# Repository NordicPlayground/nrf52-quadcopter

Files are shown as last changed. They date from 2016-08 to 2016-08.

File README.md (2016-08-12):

# nrf52-Quadcopter

This repository contains source files for the nRF52 Quadcopter, as described in [this blog post](https://devzone.nordicsemi.com/blogs/1005/nrf52-quadcopter/) on Nordic Semiconductor's [Developer Zone](https://devzone.nordicsemi.com).

To use the firmware, you need to put in the same folder as your copy of [SDK 11.0.0](https://developer.nordicsemi.com/nRF5_SDK/).

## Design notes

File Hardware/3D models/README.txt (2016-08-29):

Regarding 3D models for nRF Quadcopter

The ducts for the propellers are modeled to fit propellers of a particular diameter (the measurement eludes me at this time), 
and the clearance between the propeller and duct wall should be as small as possible

The ducts and motor holders are modeled to be printed on a machine with some inaccuarcies, 
so the planned friction fit might not be as tight when printed on another 3D printer.
This can be fixed by either changing the 3D files themselves or adding some electrical tape around the motors.

The battery holder is supposed to attach to the pin headers under the quadcopter,
holes in the "arms" of the holder need to be drilled. Preferrably as close to 0.7 mm as possible for a tight fit.

contact: martin.sivertsen@gmail.com

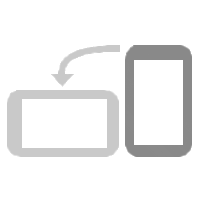
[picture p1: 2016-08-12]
Web/img/rotate.png

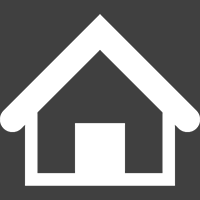
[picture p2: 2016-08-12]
Web/img/home.png

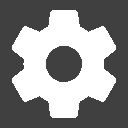
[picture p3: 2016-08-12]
Web/img/settings.png

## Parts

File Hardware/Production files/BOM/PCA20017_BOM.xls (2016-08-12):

Bill of material
PCB: | PCA20017
Version: | 1.0.0
Designator | Value | Description | Footprint Doc | Manufacturer | Manufacturer Part Number
A1 | 2450AT18B100 | 2.45 GHz chip antenna | 2450AT18B100 | Johanson Technology | 2450AT18B100
BAT | B2B-ZR | CONN JST 2POS 0.059" (1.50mm) | B2B-ZR | JST Sales America Inc | B2B-ZR(LF)(SN)
C1, C2, C11, C12 | 12pF | Capacitor, NP0, ±2% | 0402
C3 | 0.8pF | Capacitor, NP0, ±5% | 0402
C4, C5, C8, C15, C19, C21, C22, C23, C25, C26, C30, C32 | 100nF | Capacitor, X7R, ±10% | 0402
C6 | N.C. | Not mounted | 0402
C7 | 100pF | Capacitor, NP0, ±5% | 0402
C9, C31 | 4.7µF | Capacitor, X5R, ±10% | 0603
C10 | 1.0µF | Capacitor, X7R, ±10% | 0603
C13, C14, C18 | 1.0µF | Capacitor, X5R, ±5% | 0402
C16 | 4.7µF | Capacitor, X5R, ±20% | 0402
C17 | 22µF | Capacitor, X5R, ±10% | 0805
C20 | 10µF | Capacitor, X5R, ±20% | 0603
C24 | 10nF | Capacitor, X7R, ±10% | 0402
C27, C28 | 130pF | Chip Cap 0402 | 0402
C29 | 1.2pF | Capacitor, NP0, ±0.1pF | 0402
D1, D2, D3, D4 | BAT42W | Diode Schottky, Vr=30V, If=200mA, Vf=400mV, SOD-123 | SOD-123 | Multicomp | BAT42W
D5, D6 | ZLLS410TA | DIODE SCHOTTKY 10V 0.57A SOD323 | SOD-323 | Diodes Incorporated | ZLLS410TA
J1, J2, J3, J4 | Pin List 1x2 1.27mm | Pin List 1x2, 1.27mm (50mil), N.C. | LIST_1x2_TH_1.27mm_N.C.
J6 | MicroUSB-B | MicroUSB-B-SMT | USB-Micro-B-RA-SMD-PiP | Allen Creations Corp. | AJU55-BS2111-L
L1 | 3.9nH | Inductor, 170mA, ±0.1nH | 0402 | Murata | LQP15MN3N9B02D
L2 | 10µH | Inductor, 80mA, ±10% | 0603 | Taiyo Yuden | LBMF1608T100K
L3 | 15nH | Inductor, 320mA, ±5% | 0402 | Taiyo Yuden | HK100515NJ-T
L4 | 3.3nH | Inductor, 190mA, ±0.1nH | 0402 | Murata | LQP15MN3N3B02D
L5 | 2.7nH | Inductor, 220mA, ±0.1nH | 0402 | Murata | LQP15MN2N7B02D
LD1, LD1B, LD2, LD2B, LD3, LD3B, LD4, LD4B | LED RGB | RGB LED 1.00 mm x 1.00 mm SMD | SML-LX0404SIUPGUSB | Lumex | SML-LX0404SIUPGUSB
Q1, Q2, Q3, Q4 | PMV31XN | N-channel TrenchMOS FET | SOT23 | NXP | PMV31XN
R1, R20, R30 | 1k | Resistor, ±1%, 0.063W | 0402
R2, R3, R6, R7 | 100R | Resistor, ±1%, 0.063W | 0402
R4, R5, R8, R9, R12, R21, R23, R25, R36 | 10k | Resistor, ±1%, 0.063W | 0402
R10, R10B, R16, R16B, R28, R28B, R33, R33B | 2k2 | Resistor, ±1%, 0.063W | 0402
R11, R11B, R17, R17B, R31, R31B, R34, R34B | 680R | Resistor, ±1%, 0.063W | 0402
R13, R14, R29 | 4k7 | Resistor, ±1%, 0.063W | 0402
R15, R15B, R18, R18B, R32, R32B, R35, R35B | 820R | Resistor, ±1%, 0.063W | 0402
R19, R22 | 12k | Resistor, ±1%, 0.063W | 0402
R24 | 150R | Resistor, ±1%, 0.063W | 0402
R37, R39 | N.C. | Not mounted | 0402
R38, R40 | 0R | Resistor, ±5%, 0.063W | 0402
SW1 | PTS840 GK SMTR LFS | Microminiature SMT Switch, Side Actuated | PTS840 Gx | C & K | PTS840 GK SMTR LFS
U1 | nRF52832-QFAA | Multi-protocol Bluetooth Low Energy, ANT and 2.4GHz proprietary system-on-chip | QFN-48 | Nordic Semiconductor | nRF52832-QFAA
U2 | MPU-9250 | 9-axis MotionTracking™ Device | QFN-24 | InvenSense | MPU-9250
U3 | MS5611-01BA03 | Accurate Pressure/Altitude and Temperature sensor with I2C and SPI interface | QFN-8 | Measurement Specialties | MS561101BA03-50
U4 | BQ24075 | IC SINGLE CELL USB LI-ION CHARGER | S-PVQFN-N16 | Texas Instruments | BQ24075RGTT
U5 | MAX17043 | IC FUEL FUAGE LI-ION | TDFN-8L-2x3mm | Maxim | MAX17043G+U
U6 | PCAL6408A | 8-bit I2C-bus I/O expander with interrupt output | XQFN-16 | NXP Semiconductors | PCAL6408AHK
U7 | TLV70230DBVT | IC REG LDO 3V 300MA SOT23-5 | SOT-23-5 | Texas Instruments | TLV70230DBVT
U8 | 24AA64F | IC EEPROM 64K with I2C interface TDFN-8 | TDFN-8 | Microchip | 24AA64T-I/MNY
U9 | LPS25H | MEMS pressure sensor: 260-1260 hPa absolute digital output barometer | HCLGA-10L | STMicroelectronics | LPS25H
X1 | 32MHz | XTAL SMD 2016, 32MHz, Cl=8pF, Tot: ±40ppm | XTAL_2016 | Kyocera | CX2016DB32000D0WZRC1
X2 | 32.768kHz | XTAL SMD 2012, 32.768kHz, 9pF, ±20ppm | XTAL_3215 | Seiko | SC32S-9.0PF20PPM

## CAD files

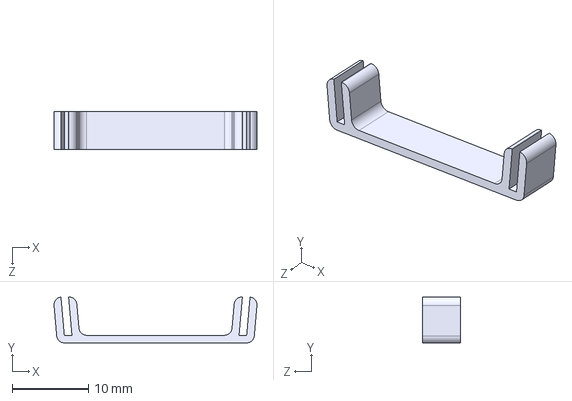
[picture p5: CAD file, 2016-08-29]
Hardware/3D models/Short duct stiffener.STEP
26.6 x 6.00 x 5.00 mm

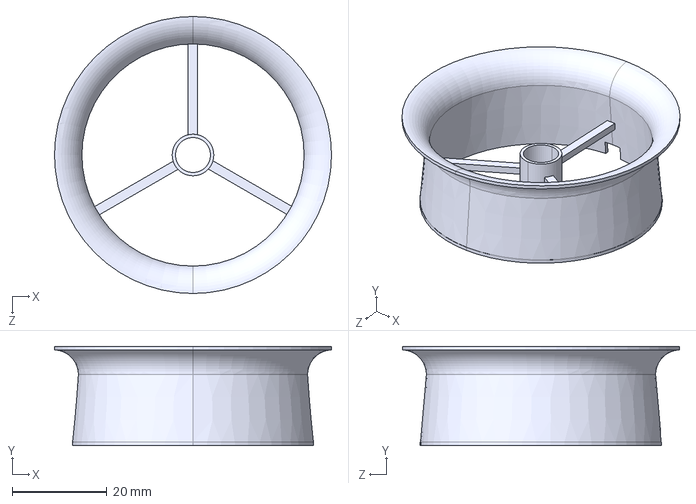
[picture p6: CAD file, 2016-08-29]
Hardware/3D models/3-blade prop and 7mm motor.STEP
58.6 x 21.0 x 58.6 mm

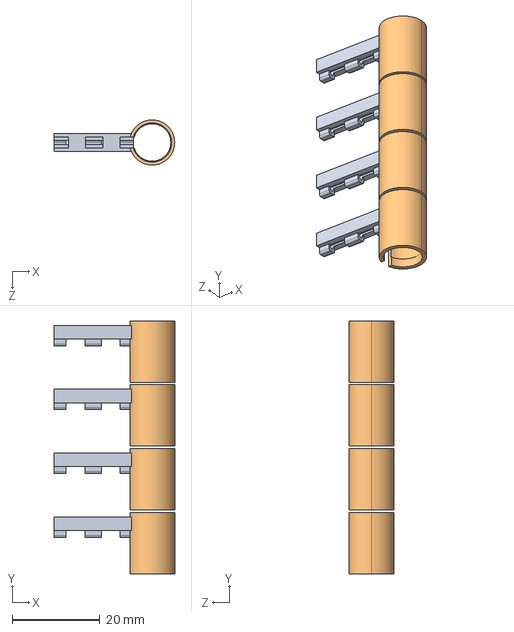
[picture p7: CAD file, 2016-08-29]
Hardware/3D models/8.5mm motorholders set of 4.STEP
27.4 x 57.5 x 10.3 mm
Arm without holder for motor x 4
Motor holder sylinder 8.45mm x 4

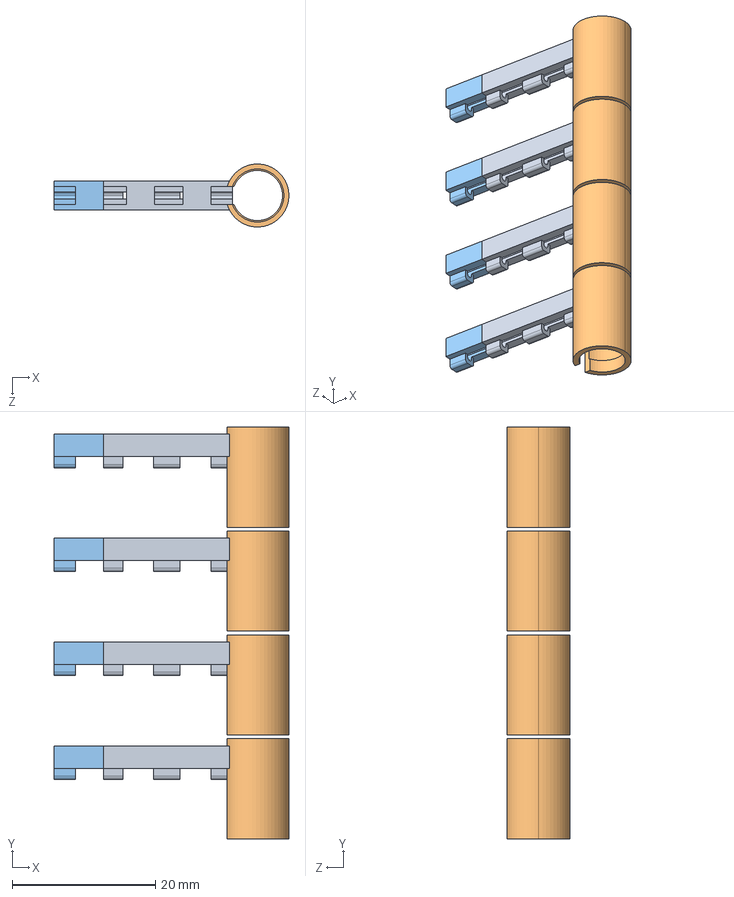
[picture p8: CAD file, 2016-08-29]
Hardware/3D models/7mm motorholders set of 4.STEP
32.8 x 57.5 x 8.79 mm
Arm without holder for motor x 4
Motor holder sylinder 7mm x 4
Arm without holder for motor extension x 4

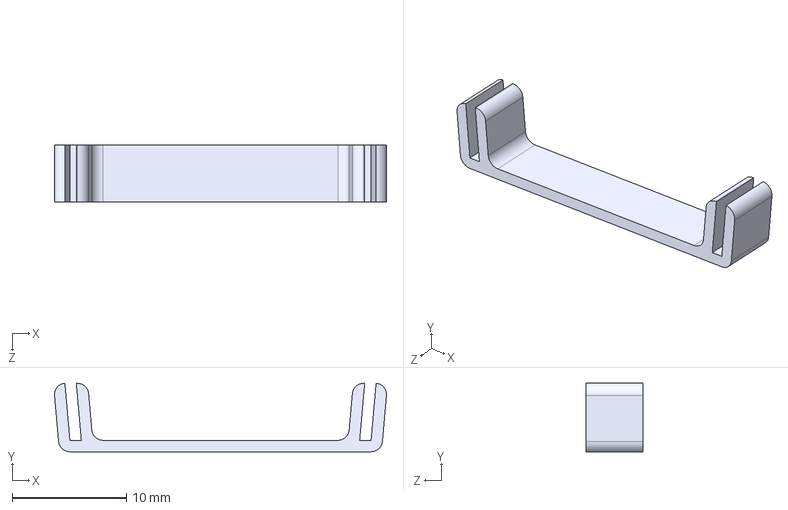
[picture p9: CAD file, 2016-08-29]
Hardware/3D models/Long duct stiffener.STEP
29.1 x 6.00 x 5.00 mm

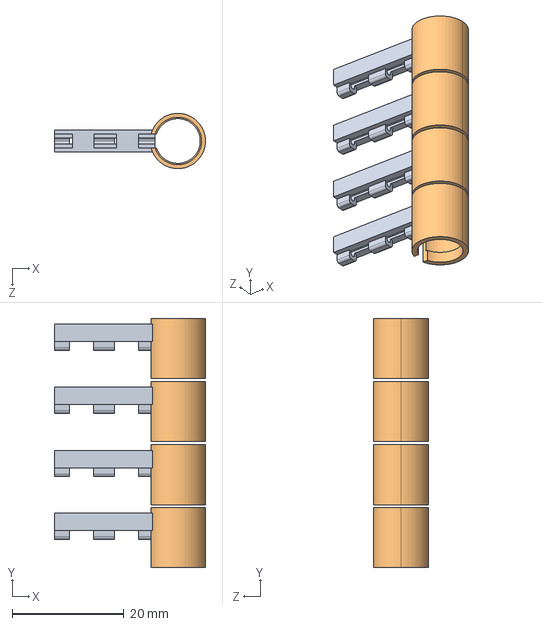
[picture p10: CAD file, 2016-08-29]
Hardware/3D models/8mm motorholders set of 4.STEP
27.0 x 44.5 x 9.90 mm
Arm without holder for motor x 4
Motor holder sylinder 8.1mm x 4

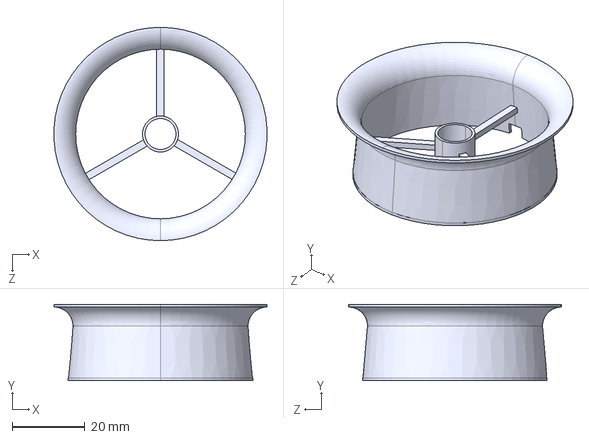
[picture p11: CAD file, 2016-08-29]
Hardware/3D models/3-blade prop and 8mm motor.STEP
58.5 x 21.0 x 58.6 mm

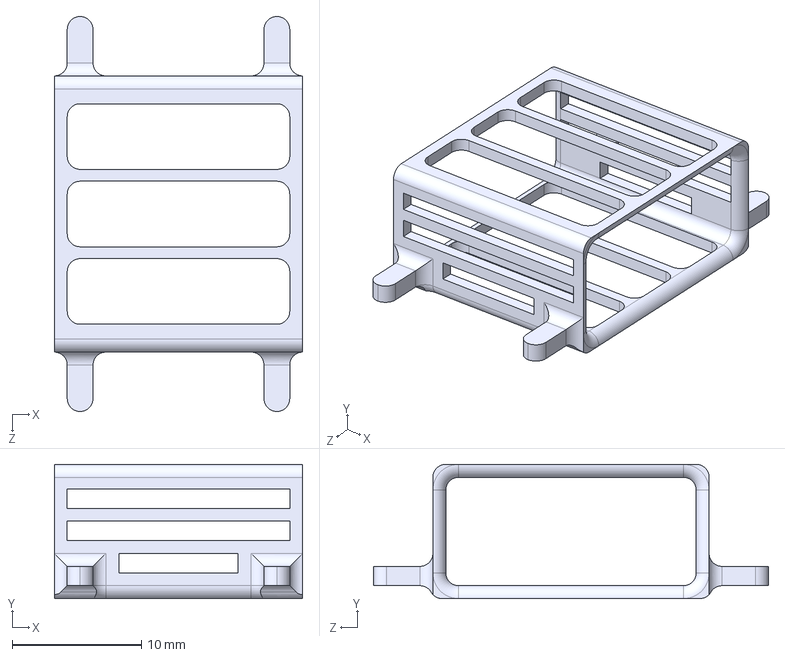
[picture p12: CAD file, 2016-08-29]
Hardware/3D models/Battery holder for 380mAh 25C.STEP
19.2 x 10.4 x 30.6 mm

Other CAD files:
Hardware/3D models/Long stiffener 7mm duct.STL
Hardware/3D models/3-blade prop and 8.5mm motor.STEP
Hardware/3D models/3-blade prop and 7mm motor.STL
Hardware/3D models/3-blade prop and 8.5mm motor.STL
Hardware/3D models/3-blade prop and 8mm motor.STL
Hardware/3D models/7mm motorholders set of 4.STL
Hardware/3D models/8.5 mm motorholders set of 4.STL
Hardware/3D models/8mm motorholders set of 4.STL
Hardware/3D models/Battery holder for 380mAh 25C.STL
Hardware/3D models/Short duct stiffener.STL

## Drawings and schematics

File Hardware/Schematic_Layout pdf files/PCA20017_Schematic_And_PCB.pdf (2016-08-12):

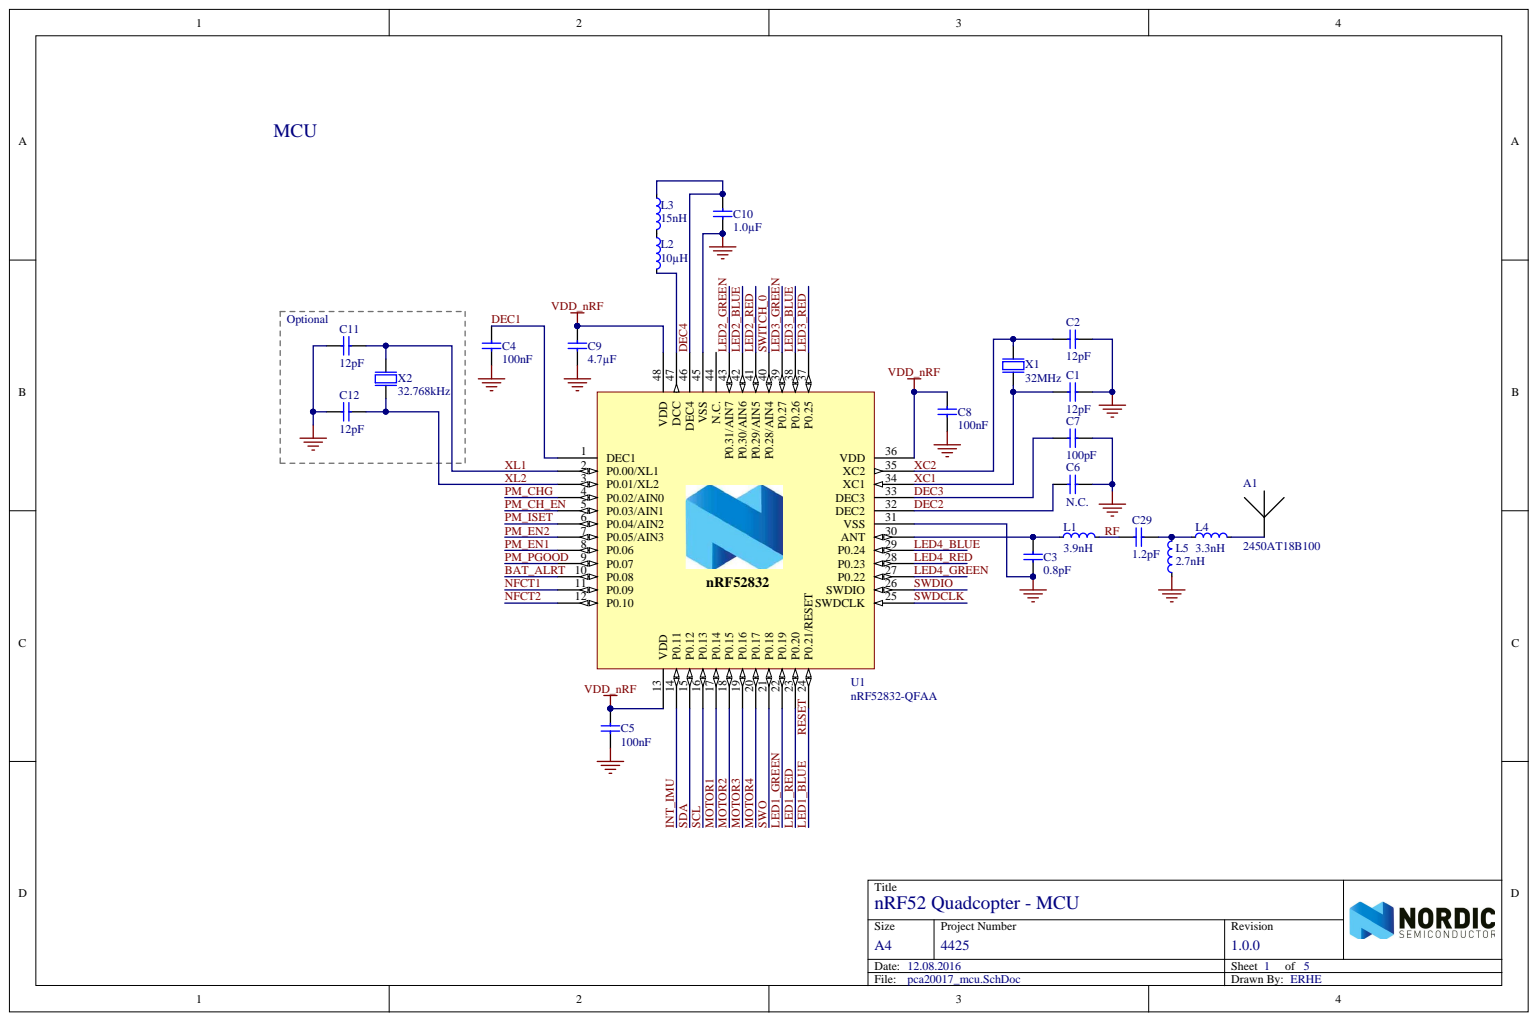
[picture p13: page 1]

P0.08 10 P0.09 11 P0.10 12 | | DEC3

DEC2

Title nRF52 Quadcopter - MCU

Size A4 | Project Number 4425 | Revision 1.0.0

Date: 12.08.2016 | Sheet of
File: pca20017_mcu.SchDoc | Drawn By: ERHE

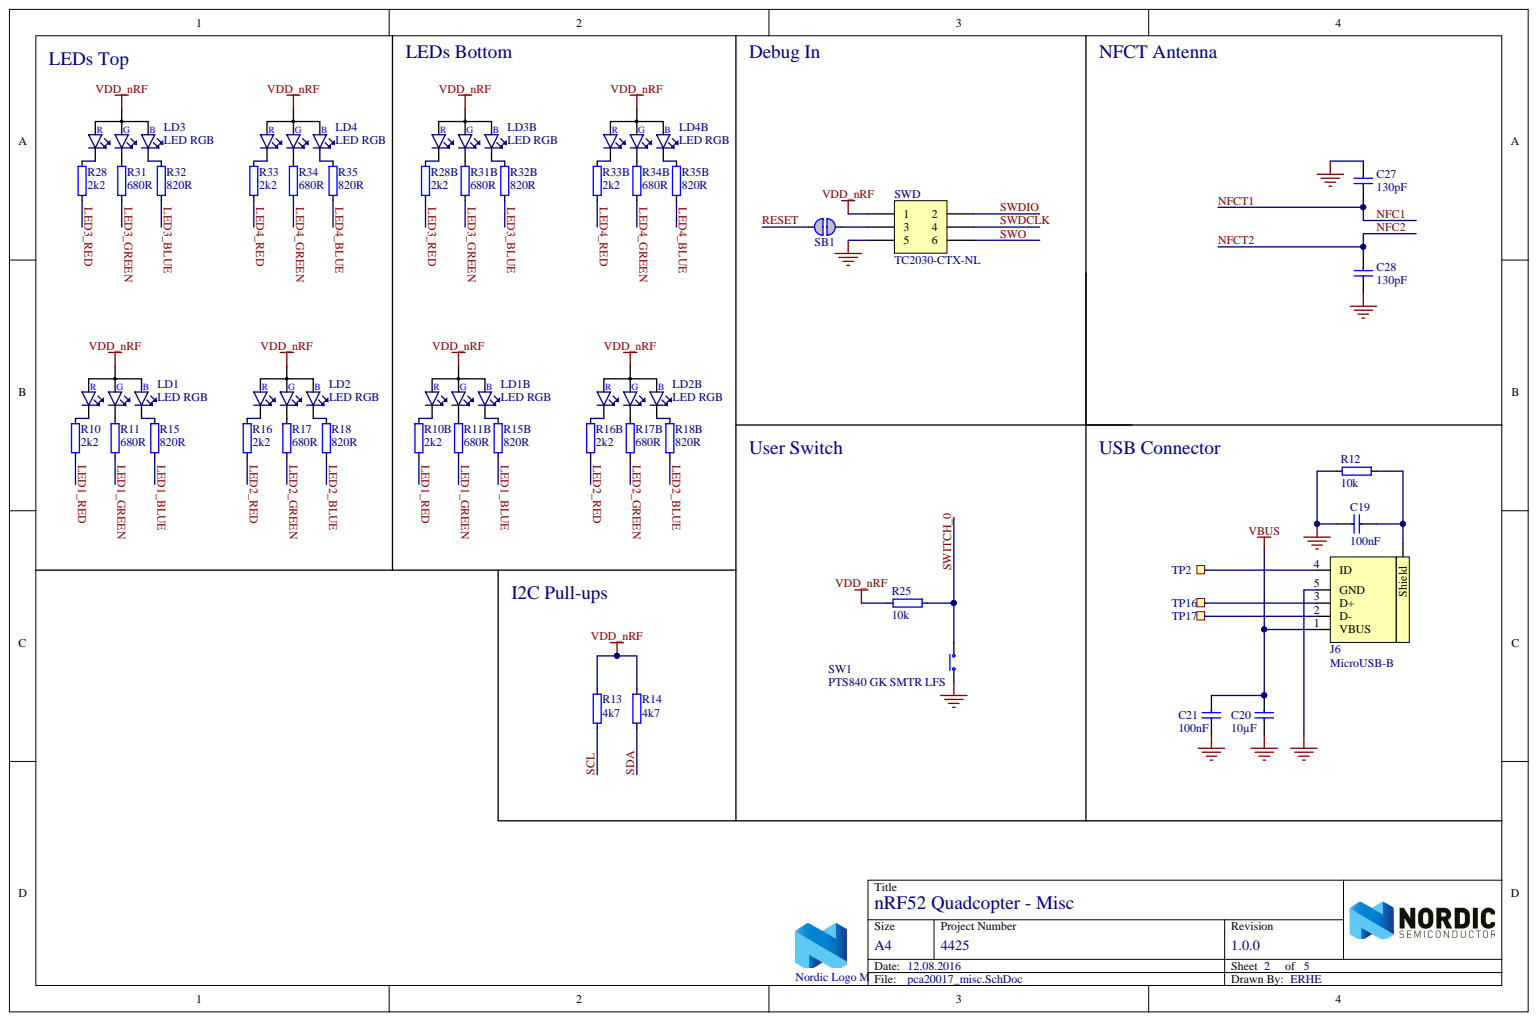
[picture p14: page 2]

ID 4
VBUS 1 D- 2 D+ 3 GND 5

Title nRF52 Quadcopter - Misc

Size A4 | Project Number 4425 | Revision 1.0.0

pca20017_misc.SchDoc

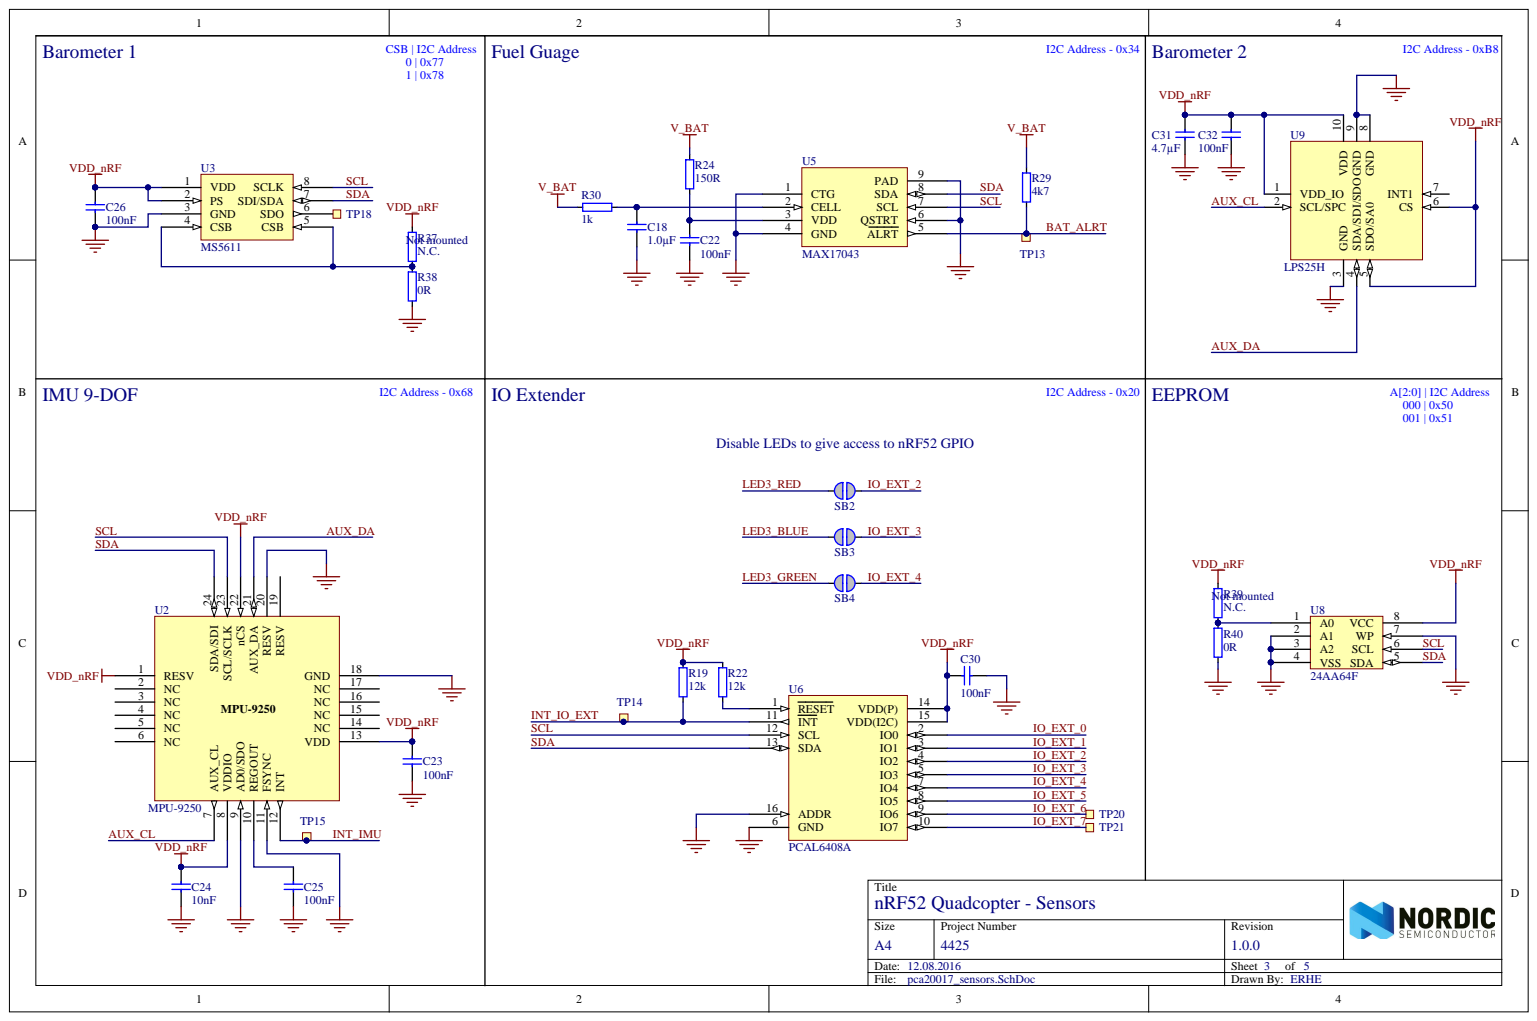
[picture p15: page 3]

SDO/SA0 5 SDA/SDI/SDO 4

VDD_IO 1

VDD 3

Disable LEDs to give access to nRF52 GPIO

Title nRF52 Quadcopter - Sensors

Size A4 | Project Number 4425 | Revision 1.0.0

pca20017_sensors.SchDoc

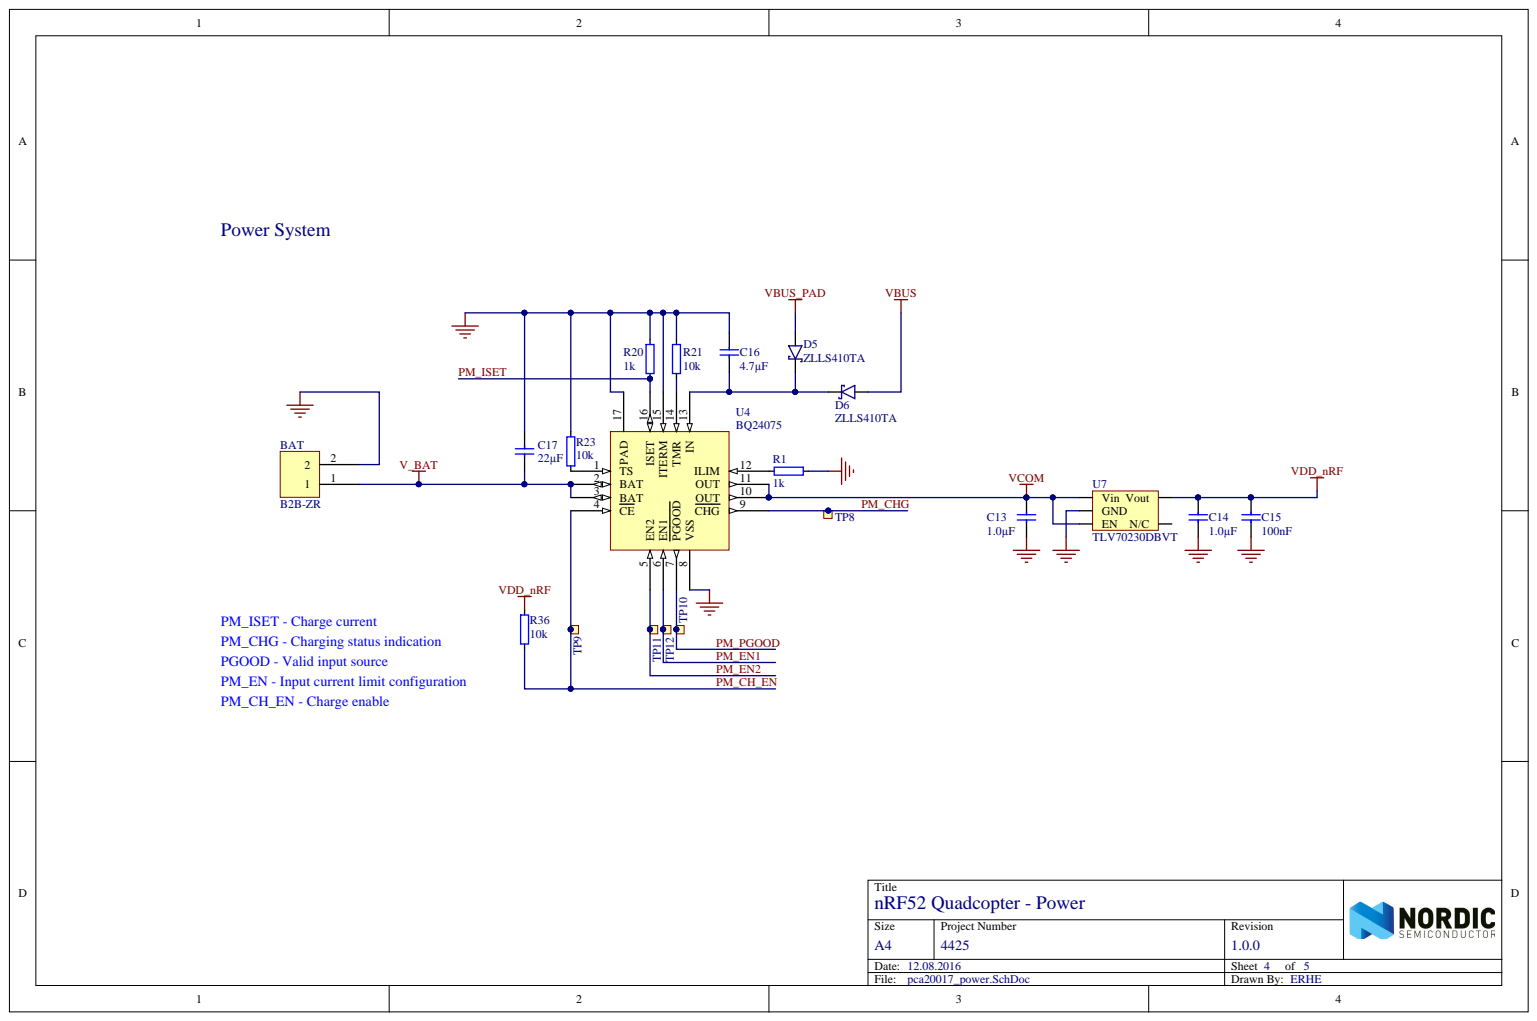
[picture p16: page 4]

IN 13 TMR 14 ITERM 15 ISET 16

PM_ISET - Charge current
PM_CHG - Charging status indication
PGOOD - Valid input source
PM_EN - Input current limit configuration
PM_CH_EN - Charge enable

Title nRF52 Quadcopter - Power

Size A4 | Project Number 4425 | Revision 1.0.0

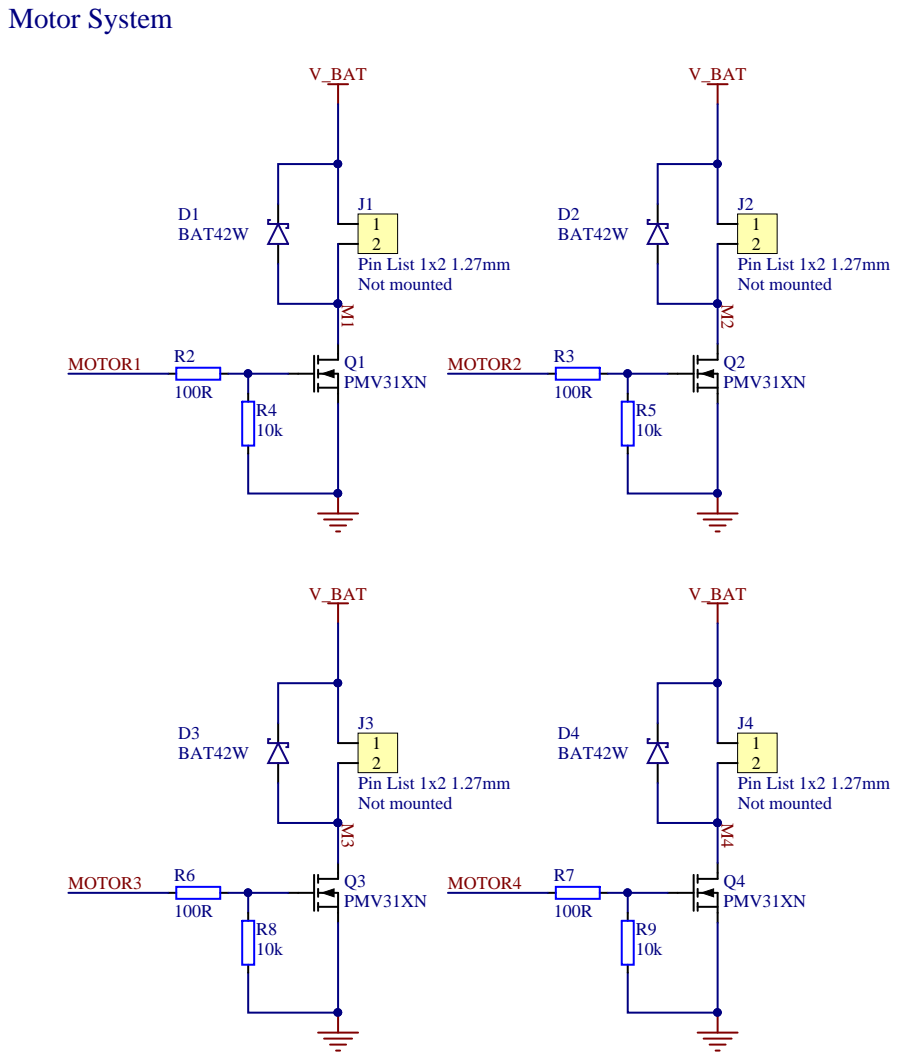
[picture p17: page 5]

Title nRF52 Quadcopter - Motors

Size A4 | Project Number 4425 | Revision 1.0.0

pca20017_motors.SchDoc

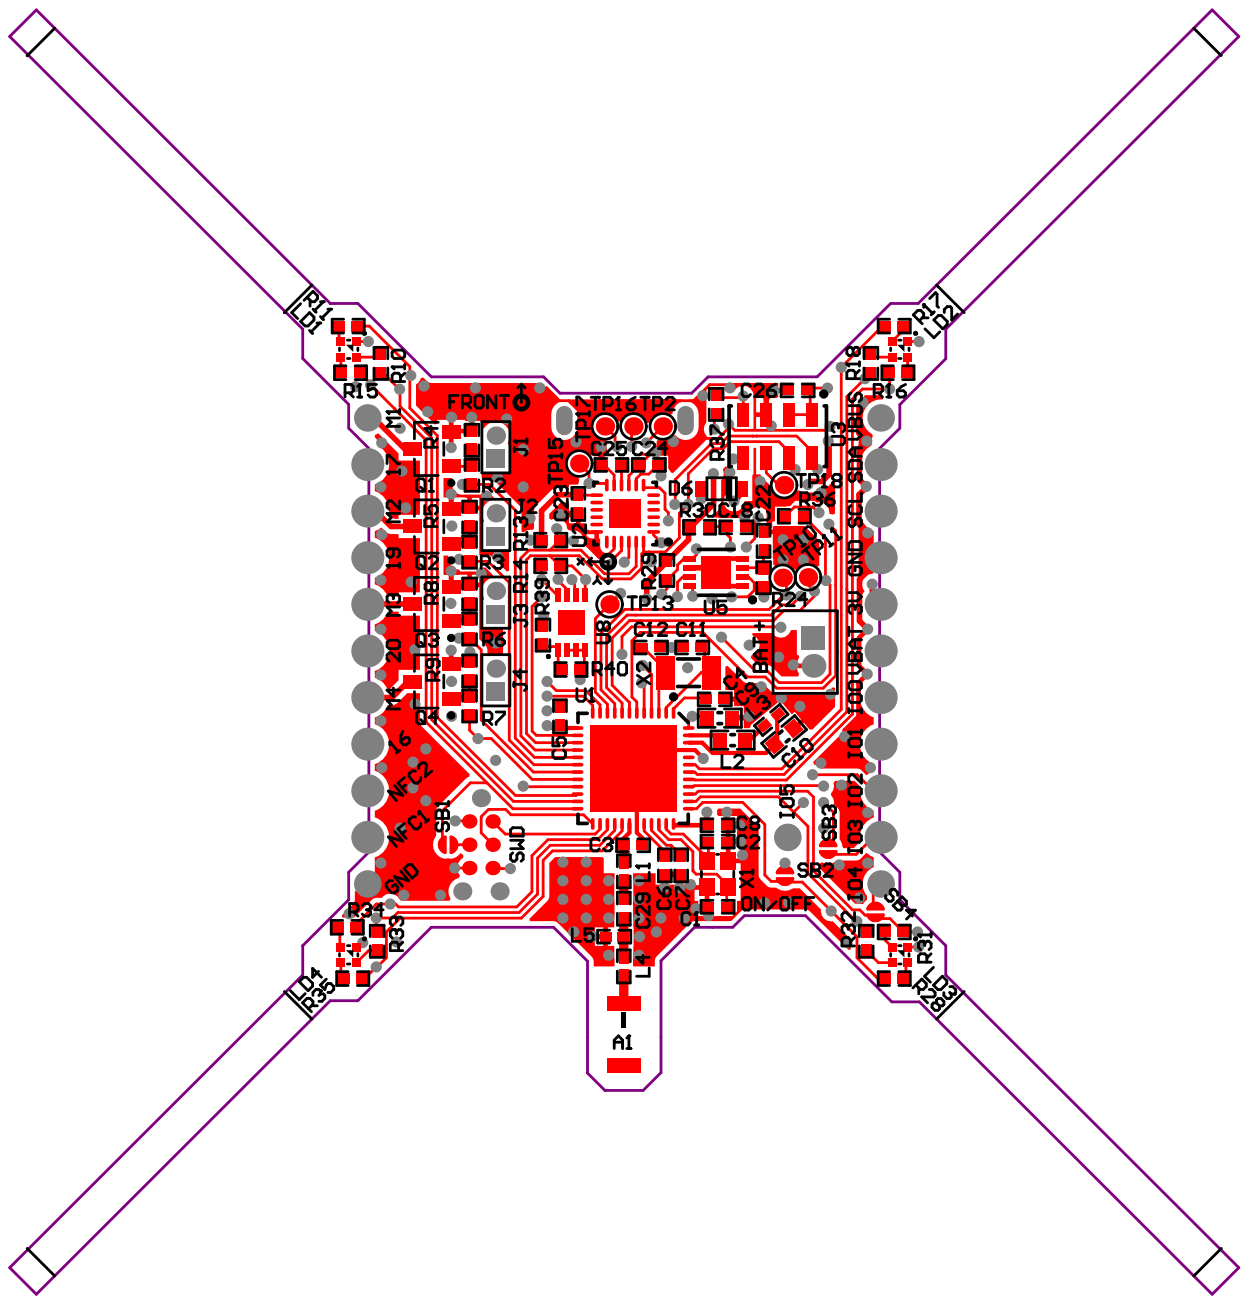
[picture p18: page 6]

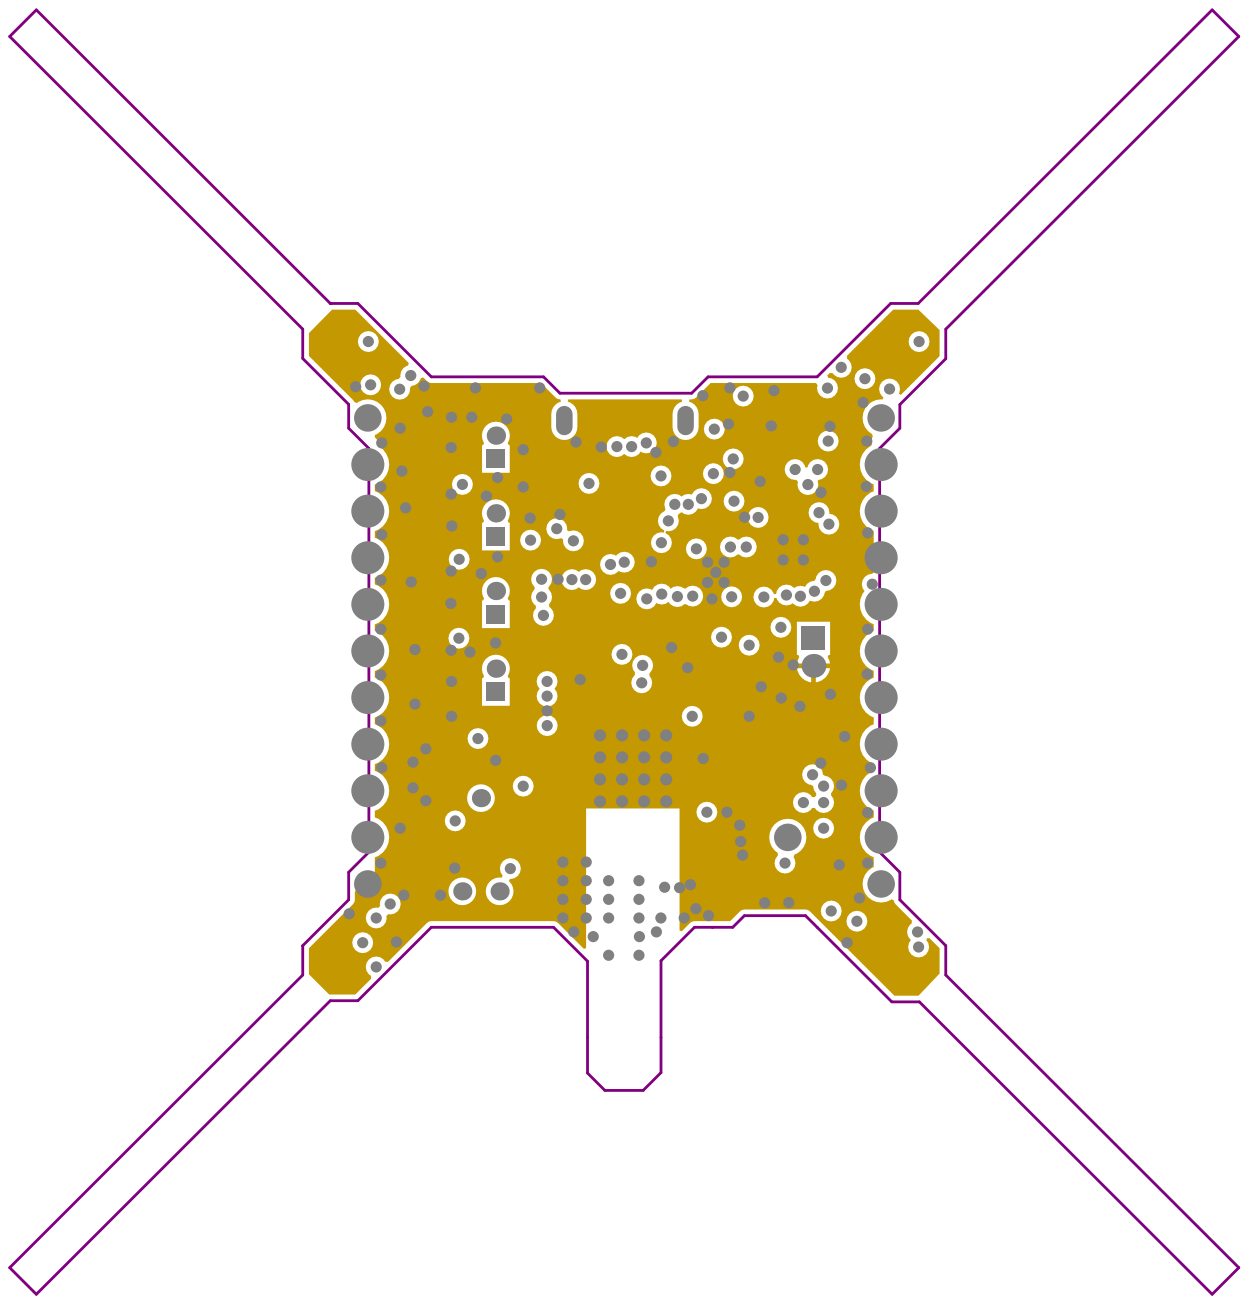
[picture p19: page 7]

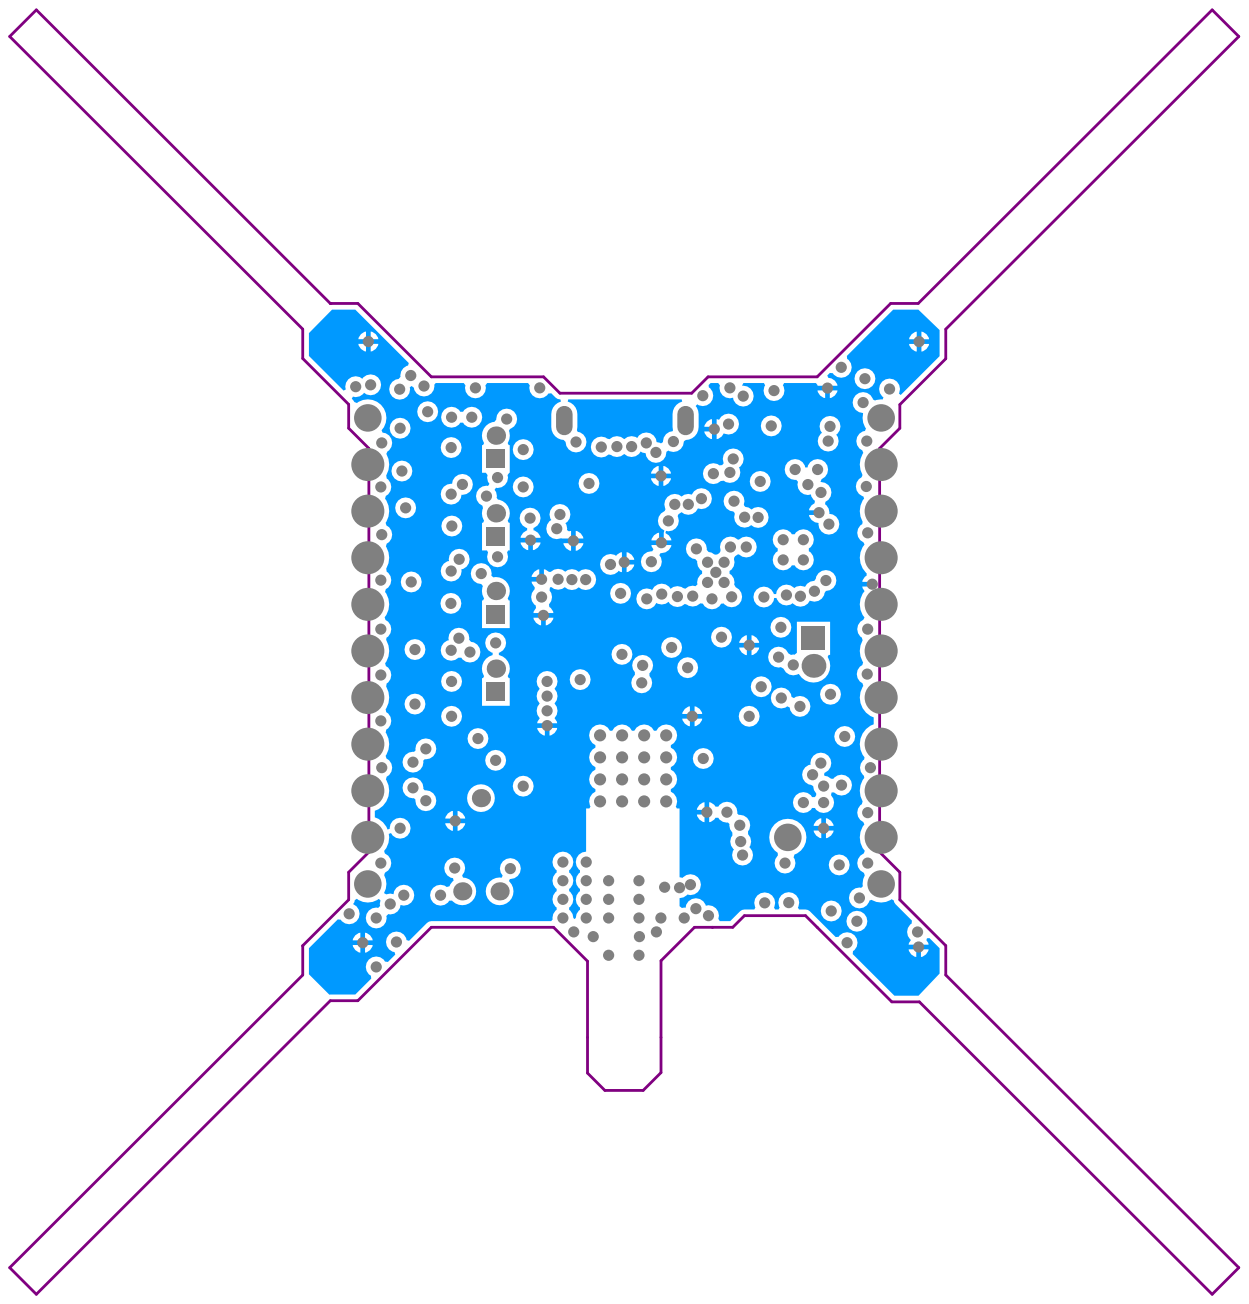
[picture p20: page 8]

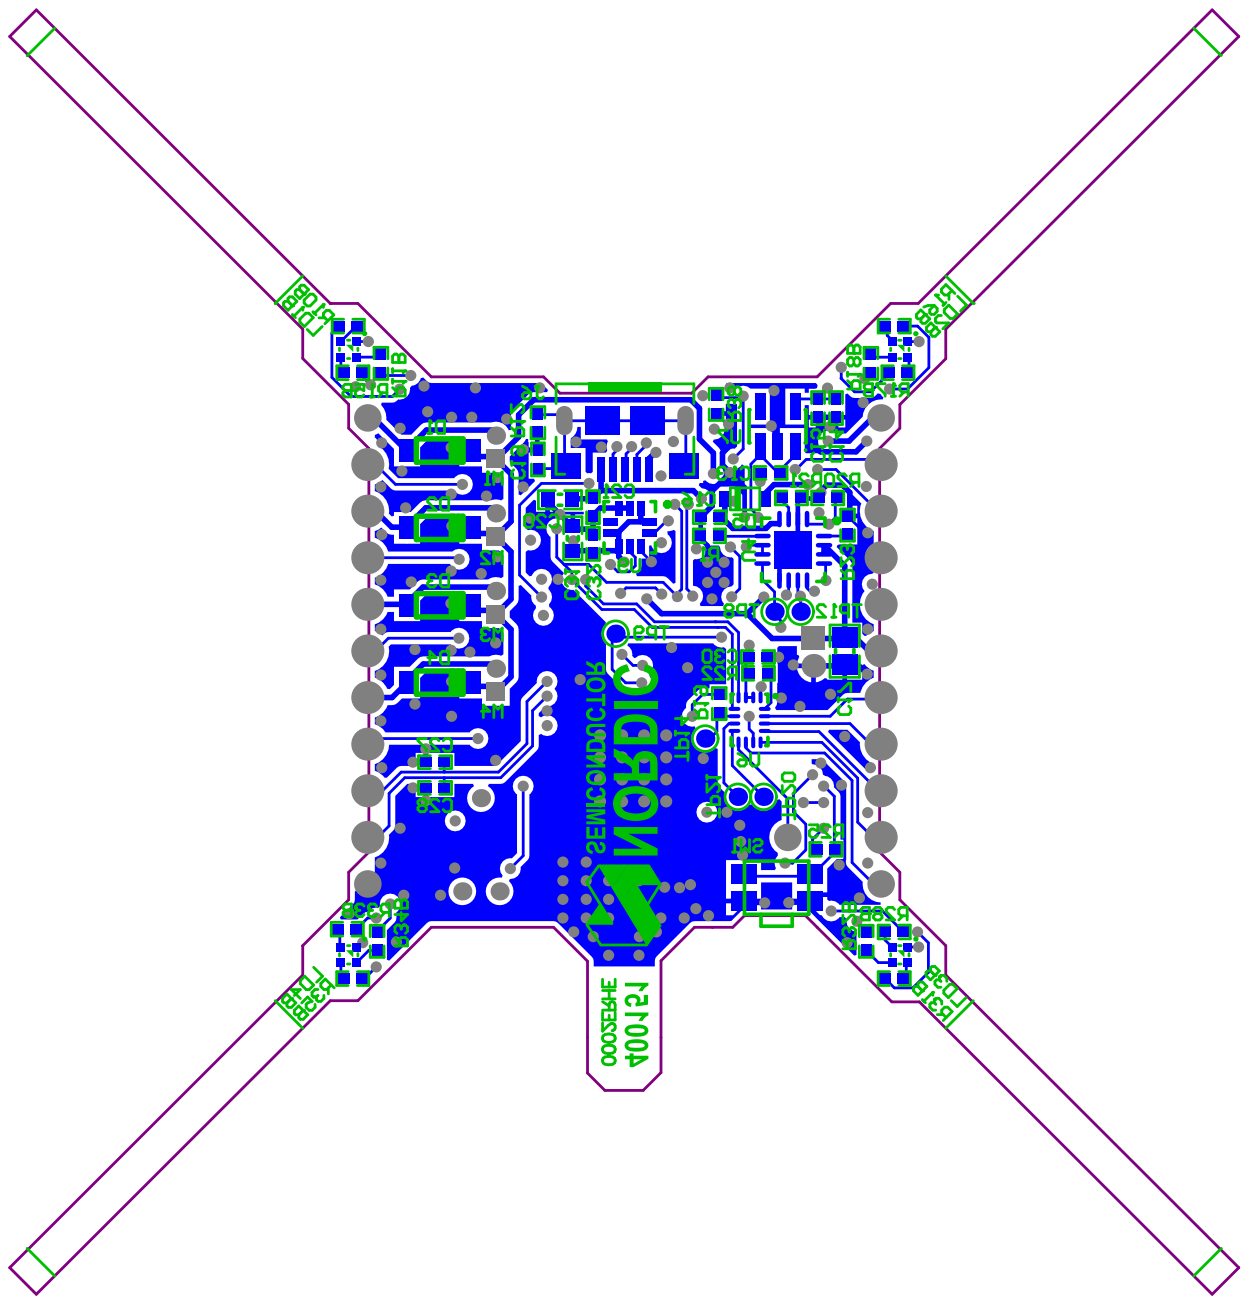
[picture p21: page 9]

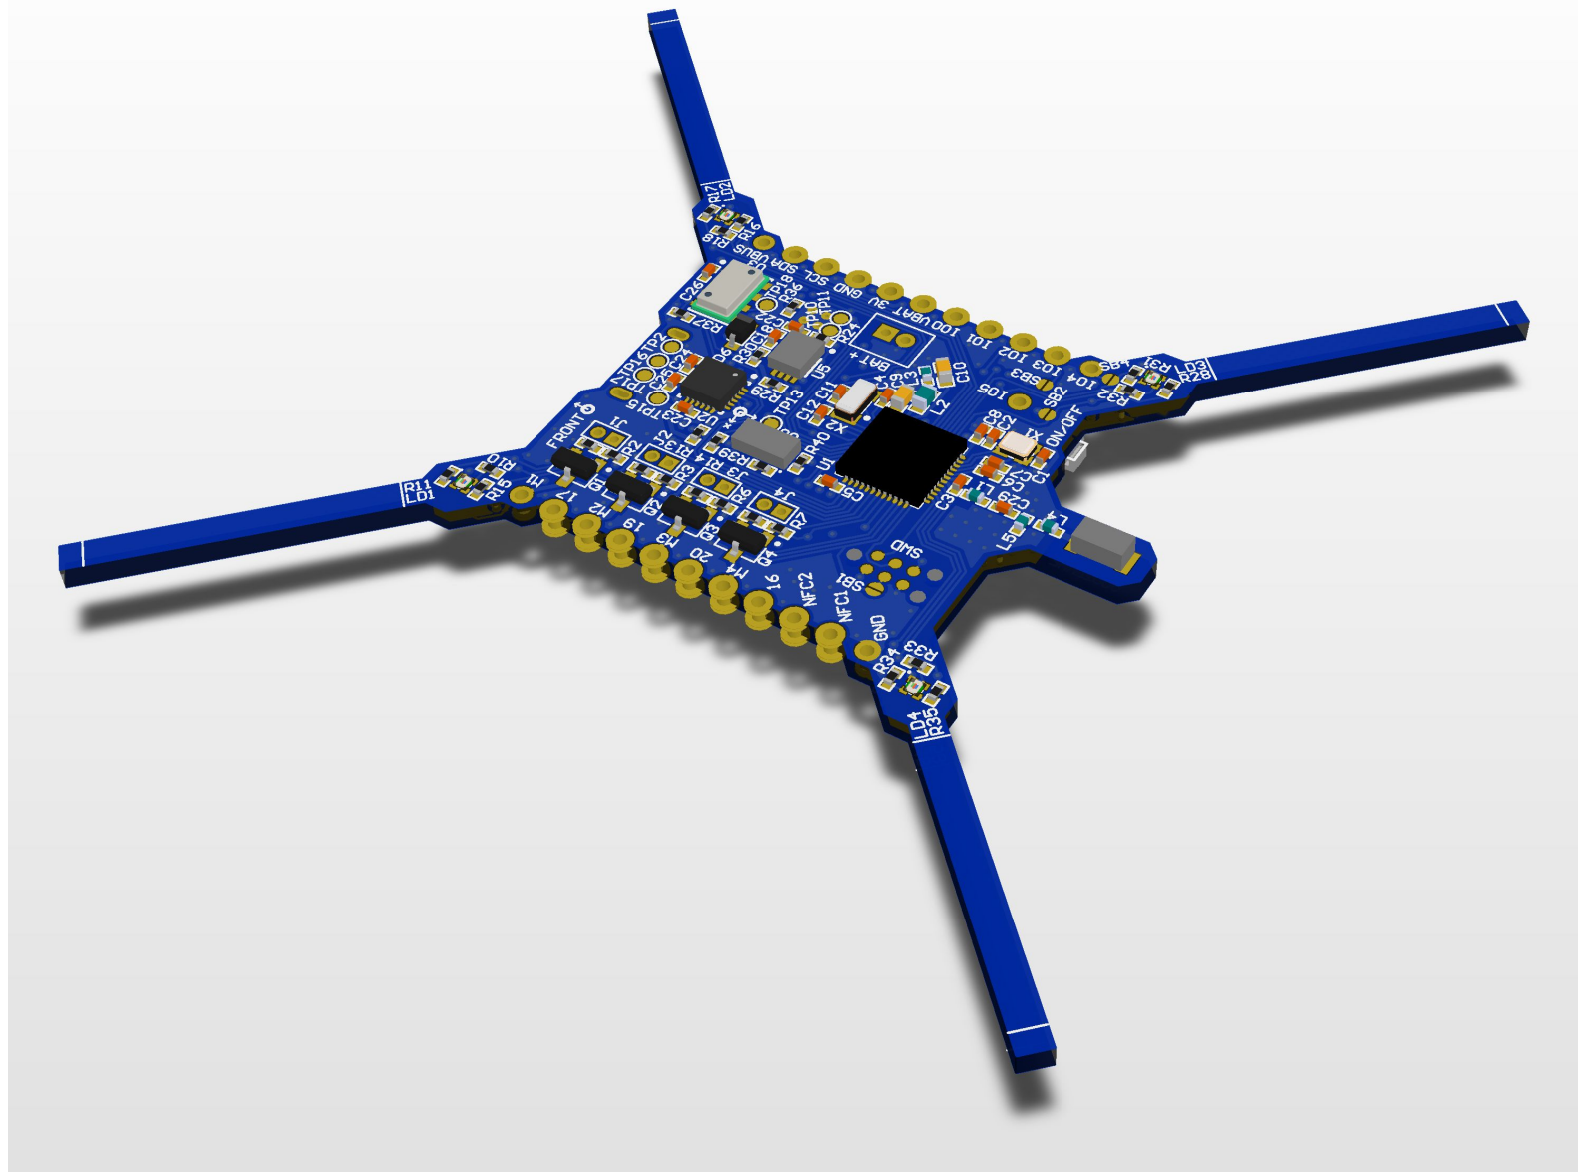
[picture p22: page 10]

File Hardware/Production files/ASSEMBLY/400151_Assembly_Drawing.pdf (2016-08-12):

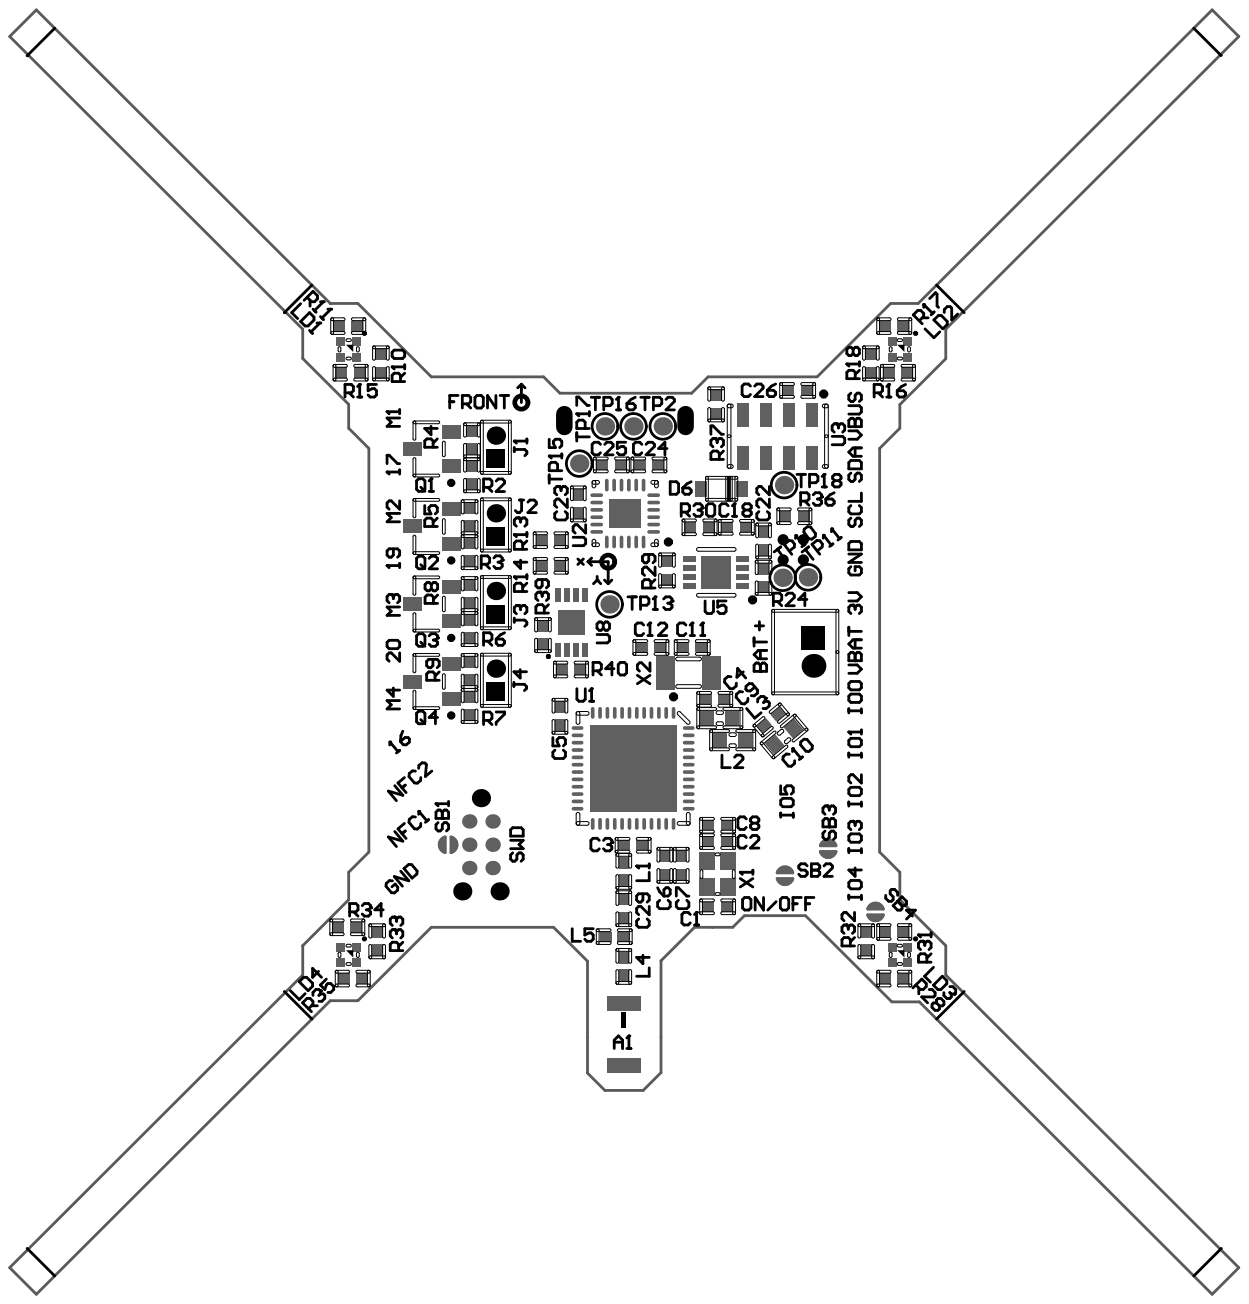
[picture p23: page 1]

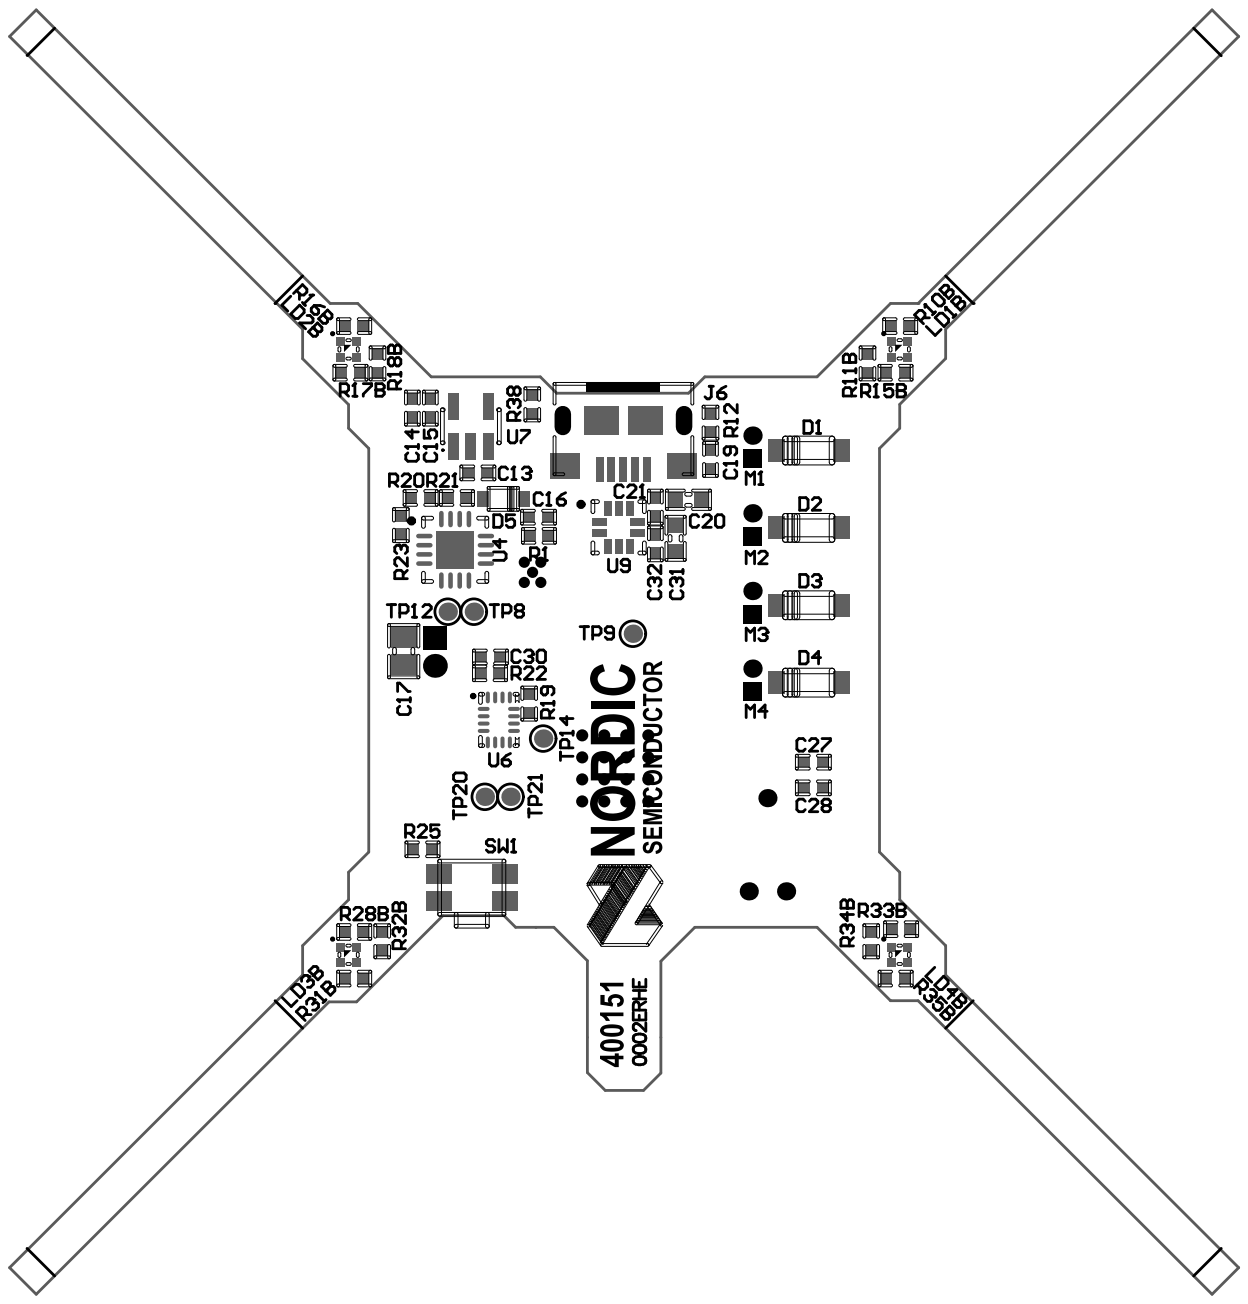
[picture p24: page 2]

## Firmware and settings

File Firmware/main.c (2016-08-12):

/* Copyright (c) 2014 Nordic Semiconductor. All Rights Reserved.
 *
 * The information contained herein is property of Nordic Semiconductor ASA.
 * Terms and conditions of usage are described in detail in NORDIC
 * SEMICONDUCTOR STANDARD SOFTWARE LICENSE AGREEMENT.
 *
 * Licensees are granted free, non-transferable use of the information. NO
 * WARRANTY of ANY KIND is provided. This heading must NOT be removed from
 * the file.
 *
 */

/** @file
 *
 * @defgroup ble_sdk_uart_over_ble_main main.c
 * @{
 * @ingroup  ble_sdk_app_nus_eval
 * @brief    UART over BLE application main file.
 *
 * This file contains the source code for a sample application that uses the Nordic UART service.
 * This application uses the @ref srvlib_conn_params module.
 */
#define BSP_DEFINES_ONLY //DEBUG
#include <stdint.h>
#include <string.h>
#include "nordic_common.h"
#include "nrf.h"
#include "ble_hci.h"
#include "ble_advdata.h"
#include "ble_advertising.h"
#include "ble_conn_params.h"
#include "softdevice_handler.h"
#include "app_timer.h"
#include "app_button.h"
#include "ble_nus.h"
#include "app_uart.h"
#include "app_util_platform.h"
#include "bsp.h"
#include "bsp_btn_ble.h"
#include "nrf_gpio.h"
#include "sensfusion6.h"

#include "i2cdev.h"
#include "pstorage.h"


#include "controller.h"
#include "stabilizer.h"
#include "command_input.h"
#include "motor.h"
#include "quadcopter.h"
#include "imu_toplevel.h"
#include "ble_radio_notification.h"
#include "advertising.h"
#include "pm.h"
#include "max17043.h"
#include "ms5611.h"

#include "printing.h"

#define IS_SRVC_CHANGED_CHARACT_PRESENT 0                                           /**< Include the service_changed characteristic. If not enabled, the server's database cannot be changed for the lifetime of the device. */

#define CENTRAL_LINK_COUNT              0                                           /**<number of central links used by the application. When changing this number remember to adjust the RAM settings*/
#define PERIPHERAL_LINK_COUNT           1                                           /**<number of peripheral links used by the application. When changing this number remember to adjust the RAM settings*/

#define DEVICE_NAME                     "nrfRacer"                                  /**< Name of device. Will be included in the advertising data. */
#define NUS_SERVICE_UUID_TYPE           BLE_UUID_TYPE_VENDOR_BEGIN                  /**< UUID type for the Nordic UART Service (vendor specific). */

#define APP_ADV_INTERVAL                MSEC_TO_UNITS(100, UNIT_0_625_MS)         /**< The advertising interval (in units of 0.625 ms. This value corresponds to 40 ms). */
#define APP_ADV_TIMEOUT_IN_SECONDS      0                                         /**< The advertising timeout (in units of seconds). */

#define APP_TIMER_PRESCALER             0                                           /**< Value of the RTC1 PRESCALER register. */
#define APP_TIMER_OP_QUEUE_SIZE         7                                           /**< Size of timer operation queues. */

#define MIN_CONN_INTERVAL               MSEC_TO_UNITS(20, UNIT_1_25_MS)             /**< Minimum acceptable connection interval (20 ms), Connection interval uses 1.25 ms units. */
#define MAX_CONN_INTERVAL               MSEC_TO_UNITS(20, UNIT_1_25_MS)             /**< Maximum acceptable connection interval (75 ms), Connection interval uses 1.25 ms units. */
#define SLAVE_LATENCY                   0                                           /**< Slave latency. */
#define CONN_SUP_TIMEOUT                MSEC_TO_UNITS(200, UNIT_10_MS)             /**< Connection supervisory timeout (4 seconds), Supervision Timeout uses 10 ms units. */
#define FIRST_CONN_PARAMS_UPDATE_DELAY  APP_TIMER_TICKS(5000, APP_TIMER_PRESCALER)  /**< Time from initiating event (connect or start of notification) to first time sd_ble_gap_conn_param_update is called (5 seconds). */
#define NEXT_CONN_PARAMS_UPDATE_DELAY   APP_TIMER_TICKS(30000, APP_TIMER_PRESCALER) /**< Time between each call to sd_ble_gap_conn_param_update after the first call (30 seconds). */
#define MAX_CONN_PARAMS_UPDATE_COUNT    3                                           /**< Number of attempts before giving up the connection parameter negotiation. */

#define START_STRING                    "Start...\n"                                /**< The string that will be sent over the UART when the application starts. */

#define DEAD_BEEF                       0xDEADBEEF                                  /**< Value used as error code on stack dump, can be used to identify stack location on stack unwind. */

#define UART_TX_BUF_SIZE                256                                         /**< UART TX buffer size. */
#define UART_RX_BUF_SIZE                256                                         /**< UART RX buffer size. */

#define MAGIC_FLASH_BYTE 								66                                          /**< Magic byte used to recognise that flash has been written */

static ble_nus_t                        m_nus;                                      /**< Structure to identify the Nordic UART Service. */
static uint16_t                         m_conn_handle = BLE_CONN_HANDLE_INVALID;    /**< Handle of the current connection. */

static ble_uuid_t                       m_adv_uuids[] = {{0x0020, NUS_SERVICE_UUID_TYPE}};  /**< Universally unique service identifier. */

static pstorage_handle_t    m_pstorage_block_id;                                    /**< Pstorage handle for beacon params */
static pstorage_handle_t    m_pstorage_base_id;                                    /**< Pstorage handle for beacon params */


bool user_connected = false;
bool user_changed_values = false;

uint8_t pre_defined_reg_data[20];
uint8_t dummy_data[20] = {0};
uint8_t old_data = 0;

uint8_t calibration_data = 0;

uint8_t battery_level = 0;
uint8_t current_battery_level = 0;

APP_TIMER_DEF(advertising_timer);                                                   /* Defines the advertising app_timer. */

void HardFault_Handler(void)
{
	SEGGER_RTT_printf(0, "Hardfault! Stop motors!/n");
	fault_stop_motors();
}

void app_error_fault_handler(uint32_t id, uint32_t pc, uint32_t info)
{
	SEGGER_RTT_printf(0, "Application fault! Stop motors! \n");
	fault_stop_motors();

  app_error_save_and_stop(id, pc, info);

}

static void write_to_block(uint8_t *reg_data);

/**@brief Function for assert macro callback.
 *
 * @details This function will be called in case of an assert in the SoftDevice.
 *
 * @warning This handler is an example only and does not fit a final product. You need to analyse
 *          how your product is supposed to react in case of Assert.
 * @warning On assert from the SoftDevice, the system can only recover on reset.
 *
 * @param[in] line_num    Line number of the failing ASSERT call.
 * @param[in] p_file_name File name of the failing ASSERT call.
 */
void assert_nrf_callback(uint16_t line_num, const uint8_t * p_file_name)
{
    app_error_handler(DEAD_BEEF, line_num, p_file_name);
}


/**@brief Function for the GAP initialization.
 *
 * @details This function will set up all the necessary GAP (Generic Access Profile) parameters of
 *          the device. It also sets the permissions and appearance.
 */
static void gap_params_init(void)
{
    uint32_t                err_code;
    ble_gap_conn_params_t   gap_conn_params;
    ble_gap_conn_sec_mode_t sec_mode;

    BLE_GAP_CONN_SEC_MODE_SET_OPEN(&sec_mode);

    err_code = sd_ble_gap_device_name_set(&sec_mode,
                                          (const uint8_t *) DEVICE_NAME,
                                          strlen(DEVICE_NAME));
    APP_ERROR_CHECK(err_code);

    memset(&gap_conn_params, 0, sizeof(gap_conn_params));

    gap_conn_params.min_conn_interval = MIN_CONN_INTERVAL;
    gap_conn_params.max_conn_interval = MAX_CONN_INTERVAL;
    gap_conn_params.slave_latency     = SLAVE_LATENCY;
    gap_conn_params.conn_sup_timeout  = CONN_SUP_TIMEOUT;

    err_code = sd_ble_gap_ppcp_set(&gap_conn_params);
    APP_ERROR_CHECK(err_code);
}

/**@brief Function for handling the data from the Nordic UART Service.
 *
 * @details This function will process the data received from the Nordic UART BLE Service and send
 *          it to the UART module.
 *
 * @param[in] p_nus    Nordic UART Service structure.
 * @param[in] p_data   Data to be send to UART module.
 * @param[in] length   Length of the data.
 */
/**@snippet [Handling the data received over BLE] */
static void nus_data_handler(ble_nus_t * p_nus, uint8_t * p_data, uint16_t length)
{
	p_data[19] = MAGIC_FLASH_BYTE;
	
	static uint32_t data[20/sizeof(uint32_t)];
	uint8_t * p_dat = (uint8_t *) data;
	
	memcpy(data, p_data, length);
   //Update regulator parameters
		update_reg_param(p_data);
	  write_to_block(p_dat);
}

static void control_char_write_handler(ble_nus_t * p_nus, uint8_t * p_data, uint16_t length)
{
	//if (p_data[19] == old_data)
		fail_safe_handler();
	//else{
		set_attitude_setpoints(p_data);
		cmd_set_reg_mode(p_data);
	
		if (calibration_data != p_data[10]){
			set_calibration();
			calibration_data = p_data[10];
		}
		old_data = p_data[19];
		set_user_control();
	//}
}
/**@snippet [Handling the data received over BLE] */


/**@brief Function for initializing services that will be used by the application.
 */
static void services_init(void)
{
    uint32_t       err_code;
    ble_nus_init_t nus_init;

    memset(&nus_init, 0, sizeof(nus_init));

    nus_init.data_handler = nus_data_handler;
	  nus_init.data_handler_ex = control_char_write_handler;

    err_code = ble_nus_init(&m_nus, &nus_init, pre_defined_reg_data);
    APP_ERROR_CHECK(err_code);
}


/**@brief Function for handling an event from the Connection Parameters Module.
 *
 * @details This function will be called for all events in the Connection Parameters Module
 *          which are passed to the application.
 *
 * @note All this function does is to disconnect. This could have been done by simply setting
 *       the disconnect_on_fail config parameter, but instead we use the event handler
 *       mechanism to demonstrate its use.
 *
 * @param[in] p_evt  Event received from the Connection Parameters Module.
 */
static void on_conn_params_evt(ble_conn_params_evt_t * p_evt)
{
    uint32_t err_code;

    if(p_evt->evt_type == BLE_CONN_PARAMS_EVT_FAILED)
    {

        err_code = sd_ble_gap_disconnect(m_conn_handle, BLE_HCI_CONN_INTERVAL_UNACCEPTABLE);

        APP_ERROR_CHECK(err_code);
    }
}


/**@brief Function for handling errors from the Connection Parameters module.
 *
 * @param[in] nrf_error  Error code containing information about what went wrong.
 */
static void conn_params_error_handler(uint32_t nrf_error)
{
    APP_ERROR_HANDLER(nrf_error);
}


/**@brief Function for initializing the Connection Parameters module.
 */
static void conn_params_init(void)
{
    uint32_t               err_code;
    ble_conn_params_init_t cp_init;

    memset(&cp_init, 0, sizeof(cp_init));

    cp_init.p_conn_params                  = NULL;
    cp_init.first_conn_params_update_delay = FIRST_CONN_PARAMS_UPDATE_DELAY;
    cp_init.next_conn_params_update_delay  = NEXT_CONN_PARAMS_UPDATE_DELAY;
    cp_init.max_conn_params_update_count   = MAX_CONN_PARAMS_UPDATE_COUNT;
    cp_init.start_on_notify_cccd_handle    = BLE_GATT_HANDLE_INVALID;
    cp_init.disconnect_on_fail             = false;
    cp_init.evt_handler                    = on_conn_params_evt;
    cp_init.error_handler                  = conn_params_error_handler;

    err_code = ble_conn_params_init(&cp_init);
    APP_ERROR_CHECK(err_code);
}


/**@brief Function for putting the chip into sleep mode.
 *
 * @note This function will not return.
 */
static void sleep_mode_enter(void)
{
    uint32_t err_code = NRF_SUCCESS;
    //uint32_t err_code = bsp_indication_set(BSP_INDICATE_IDLE);
    APP_ERROR_CHECK(err_code);

    // Prepare wakeup buttons.
    //err_code = bsp_btn_ble_sleep_mode_prepare();
    APP_ERROR_CHECK(err_code);

    // Go to system-off mode (this function will not return; wakeup will cause a reset).
    err_code = sd_power_system_off();
    APP_ERROR_CHECK(err_code);
}


/**@brief Function for handling advertising events.
 *
 * @details This function will be called for advertising events which are passed to the application.
 *
 * @param[in] ble_adv_evt  Advertising event.
 */
static void on_adv_evt(ble_adv_evt_t ble_adv_evt)
{
    //uint32_t err_code;

    switch (ble_adv_evt)
    {
        case BLE_ADV_EVT_FAST:
            //err_code = bsp_indication_set(BSP_INDICATE_ADVERTISING);
            //APP_ERROR_CHECK(err_code);
            break;
        case BLE_ADV_EVT_IDLE:
            sleep_mode_enter();
            break;
        default:
            break;
    }
}

void set_reg_param(uint8_t *block_data){

	  pre_defined_reg_data[0] = battery_level;

	  pre_defined_reg_data[1] = block_data[1];
	  pre_defined_reg_data[2] = block_data[2];
	  pre_defined_reg_data[3] = block_data[3];

	  pre_defined_reg_data[4] = block_data[4];
	  pre_defined_reg_data[5] = block_data[5];
	  pre_defined_reg_data[6] = block_data[6];

	  pre_defined_reg_data[7] = block_data[7];
	  pre_defined_reg_data[8] = block_data[8];
	  pre_defined_reg_data[9] = block_data[9];

    pre_defined_reg_data[10] = block_data[10];
    pre_defined_reg_data[11] = block_data[11];
  	pre_defined_reg_data[12] = block_data[12];

  	pre_defined_reg_data[13] = block_data[13];
  	pre_defined_reg_data[14] = block_data[14];
  	pre_defined_reg_data[15] = block_data[15];

  	pre_defined_reg_data[16] = block_data[16];
  	pre_defined_reg_data[17] = block_data[17];
  	pre_defined_reg_data[18] = block_data[18];
		
		update_reg_param(pre_defined_reg_data);
}


void send_battery_level(uint8_t battery_level_percent){
	pre_defined_reg_data[0] = battery_level_percent;
	ble_nus_string_send(&m_nus, pre_defined_reg_data, sizeof(pre_defined_reg_data));
}

/**@brief Function for the application's SoftDevice event handler.
 *
 * @param[in] p_ble_evt SoftDevice event.
 */
static void on_ble_evt(ble_evt_t * p_ble_evt)
{
    uint32_t                         err_code;

    switch (p_ble_evt->header.evt_id)
    {
        case BLE_GAP_EVT_CONNECTED:
            //err_code = bsp_indication_set(BSP_INDICATE_CONNECTED);
            //APP_ERROR_CHECK(err_code);
            m_conn_handle = p_ble_evt->evt.gap_evt.conn_handle;
            NRF_LOG_PRINTF("BLE_GAP_EVT_CONNECTED\n");
				    set_calibration();
				    user_connected = true;
						set_user_control();
				    led_connected();
            break;

        case BLE_GAP_EVT_DISCONNECTED:
            //err_code = bsp_indication_set(BSP_INDICATE_IDLE);
            //APP_ERROR_CHECK(err_code);
            m_conn_handle = BLE_CONN_HANDLE_INVALID;
            NRF_LOG_PRINTF("DC %d\n",p_ble_evt->evt.gap_evt.params.disconnected.reason);

				    user_connected = false;
            led_config();
				    fail_safe_handler();
            set_attitude_setpoints(dummy_data);
            break;

				case BLE_GAP_EVT_TIMEOUT:
            m_conn_handle = BLE_CONN_HANDLE_INVALID;
            NRF_LOG_PRINTF("Timeout %d\n",p_ble_evt->evt.gap_evt.params.disconnected.reason);
				
				    user_connected = false;
            led_config();
				    fail_safe_handler();
            set_attitude_setpoints(dummy_data);
						break;

        case BLE_GAP_EVT_SEC_PARAMS_REQUEST:
            // Pairing not supported
            err_code = sd_ble_gap_sec_params_reply(m_conn_handle, BLE_GAP_SEC_STATUS_PAIRING_NOT_SUPP, NULL, NULL);
            APP_ERROR_CHECK(err_code);
            break;

        case BLE_GATTS_EVT_SYS_ATTR_MISSING:
            // No system attributes have been stored.
            err_code = sd_ble_gatts_sys_attr_set(m_conn_handle, NULL, 0, 0);
            APP_ERROR_CHECK(err_code);
            break;

        default:
            // No implementation needed.
            break;
    }
}


/**@brief Function for dispatching a SoftDevice event to all modules with a SoftDevice
 *        event handler.
 *
 * @details This function is called from the SoftDevice event interrupt handler after a
 *          SoftDevice event has been received.
 *
 * @param[in] p_ble_evt  SoftDevice event.
 */
static void ble_evt_dispatch(ble_evt_t * p_ble_evt)
{
    ble_conn_params_on_ble_evt(p_ble_evt);
    ble_nus_on_ble_evt(&m_nus, p_ble_evt);
    on_ble_evt(p_ble_evt);
    ble_advertising_on_ble_evt(p_ble_evt);
    //bsp_btn_ble_on_ble_evt(p_ble_evt);

}

static void sys_evt_dispatch(uint32_t sys_evt)
{
      pstorage_sys_event_handler(sys_evt);
}


/**@brief Function for the SoftDevice initialization.
 *
 * @details This function initializes the SoftDevice and the BLE event interrupt.
 */
static void ble_stack_init(void)
{
    uint32_t err_code;

    // Initialize SoftDevice.
    nrf_clock_lf_cfg_t clock_lf_cfg = NRF_CLOCK_LFCLKSRC;
    SOFTDEVICE_HANDLER_INIT(&clock_lf_cfg, NULL);
    //SOFTDEVICE_HANDLER_INIT(NRF_CLOCK_LFCLKSRC_RC_250_PPM_TEMP_4000MS_CALIBRATION, NULL);

    ble_enable_params_t ble_enable_params;
    err_code = softdevice_enable_get_default_config(CENTRAL_LINK_COUNT,
                                                    PERIPHERAL_LINK_COUNT,
                                                    &ble_enable_params);
    APP_ERROR_CHECK(err_code);

    //Check the ram settings against the used number of links
    CHECK_RAM_START_ADDR(CENTRAL_LINK_COUNT,PERIPHERAL_LINK_COUNT);
    // Enable BLE stack.
    err_code = softdevice_enable(&ble_enable_params);
    APP_ERROR_CHECK(err_code);

    // Subscribe for BLE events.
    err_code = softdevice_ble_evt_handler_set(ble_evt_dispatch);
    APP_ERROR_CHECK(err_code);
		
		// Register with the SoftDevice handler module for BLE events.
    err_code = softdevice_sys_evt_handler_set(sys_evt_dispatch);
    APP_ERROR_CHECK(err_code); 
}


/**@brief Function for handling events from the BSP module.
 *
 * @param[in]   event   Event generated by button press.
 */
void bsp_event_handler(bsp_event_t event)
{
    uint32_t err_code;
    switch (event)
    {
        case BSP_EVENT_SLEEP:
            sleep_mode_enter();
            break;

        case BSP_EVENT_DISCONNECT:
            err_code = sd_ble_gap_disconnect(m_conn_handle, BLE_HCI_REMOTE_USER_TERMINATED_CONNECTION);
            NRF_LOG_PRINTF("DC pga bsp\n");
            //DEBUG while (1); // TODO
            if (err_code != NRF_ERROR_INVALID_STATE)
            {
                APP_ERROR_CHECK(err_code);
            }
            break;

        case BSP_EVENT_WHITELIST_OFF:
            err_code = ble_advertising_restart_without_whitelist();
            if (err_code != NRF_ERROR_INVALID_STATE)
            {
                APP_ERROR_CHECK(err_code);
            }
            break;

        default:
            break;
    }
}
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
int main(void)
{
    uint32_t err_code;

    // Initialize.

    APP_TIMER_INIT(APP_TIMER_PRESCALER, APP_TIMER_OP_QUEUE_SIZE, false);
    //uart_init();

		//Initalize peripheral functions

	  i2cdev_initialize(); /** Starts twi-driver. **/
    i2cdev_enable(true);
	  imu_init(); // Initalizes not only the imu, but every slave that contributes to stabilization on the TWI-channel.
	  pm_config(); // Sets up the charger and the fuel gauge.
    cmd_init();
	  motor_init(); //Sets up PWM for motors.
	
		led_config(); // Sets up LEDs on the quadcopter.

    // Initialize bluetooth functions

	  ble_stack_init(); //Initializes the softdevice.
		
		flash_access_init(); //Grants access to flash and the data that has been put into the pstorage block. Must be initialized befor the softdevice.
		read_from_block(); //First read from the block. Puts the read values into the RX-characteristic to be read from software.
		battery_level = max17043_get_soc(); // Reads battery level to be put into the RX-characteristic.
		
    gap_params_init();
    services_init();
    advertising_init();
	  conn_params_init();

		//Start advertising
    err_code = ble_radio_notification_init (_PRIO_APP_HIGH, NRF_RADIO_NOTIFICATION_DISTANCE_800US,on_radio_notif);
    APP_ERROR_CHECK(err_code);
    err_code = ble_advertising_start(BLE_ADV_MODE_FAST);
    APP_ERROR_CHECK(err_code);

		advertising_timer_init(); //Starts advertising timer. Switches between standard GAP-packages and eddystone-URL frames.
		
    stab_init(); //Initalizes controllers. This has to be put after the bluetooth functions have been initalized, or else the quick controller timer will conflict with the advertising timer.
    sensfusion6Init(); //Initializes the Madqwick-filter, which interpretes the raw data from the IMU.
		read_from_block(); //Reads from block yet again, to put the data read into the controllers.
		

    // Enter main loop.
    for (;;)
    {
        power_manage();
    }
}


/**
 * @}
 */

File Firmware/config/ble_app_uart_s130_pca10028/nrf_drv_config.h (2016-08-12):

/* Copyright (c) 2015 Nordic Semiconductor. All Rights Reserved.
 *
 * The information contained herein is property of Nordic Semiconductor ASA.
 * Terms and conditions of usage are described in detail in NORDIC
 * SEMICONDUCTOR STANDARD SOFTWARE LICENSE AGREEMENT.
 *
 * Licensees are granted free, non-transferable use of the information. NO
 * WARRANTY of ANY KIND is provided. This heading must NOT be removed from
 * the file.
 *
 */

#ifndef NRF_DRV_CONFIG_H
#define NRF_DRV_CONFIG_H

/**
 * Provide a non-zero value here in applications that need to use several
 * peripherals with the same ID that are sharing certain resources
 * (for example, SPI0 and TWI0). Obviously, such peripherals cannot be used
 * simultaneously. Therefore, this definition allows to initialize the driver
 * for another peripheral from a given group only after the previously used one
 * is uninitialized. Normally, this is not possible, because interrupt handlers
 * are implemented in individual drivers.
 * This functionality requires a more complicated interrupt handling and driver
 * initialization, hence it is not always desirable to use it.
 */
#define PERIPHERAL_RESOURCE_SHARING_ENABLED  0

/* CLOCK */
#define CLOCK_ENABLED 0

#if (CLOCK_ENABLED == 1)
#define CLOCK_CONFIG_XTAL_FREQ          NRF_CLOCK_XTALFREQ_Default
#define CLOCK_CONFIG_LF_SRC             NRF_CLOCK_LF_SRC_Xtal
#define CLOCK_CONFIG_IRQ_PRIORITY       APP_IRQ_PRIORITY_LOW
#endif

/* GPIOTE */
#define GPIOTE_ENABLED 1

#if (GPIOTE_ENABLED == 1)
#define GPIOTE_CONFIG_USE_SWI_EGU false
#define GPIOTE_CONFIG_IRQ_PRIORITY APP_IRQ_PRIORITY_LOW
#define GPIOTE_CONFIG_NUM_OF_LOW_POWER_EVENTS 4
#endif

/* TIMER */
#define TIMER0_ENABLED 0

#if (TIMER0_ENABLED == 1)
#define TIMER0_CONFIG_FREQUENCY    NRF_TIMER_FREQ_16MHz
#define TIMER0_CONFIG_MODE         TIMER_MODE_MODE_Timer
#define TIMER0_CONFIG_BIT_WIDTH    TIMER_BITMODE_BITMODE_32Bit
#define TIMER0_CONFIG_IRQ_PRIORITY APP_IRQ_PRIORITY_LOW

#define TIMER0_INSTANCE_INDEX      0
#endif

#define TIMER1_ENABLED 0

#if (TIMER1_ENABLED == 1)
#define TIMER1_CONFIG_FREQUENCY    NRF_TIMER_FREQ_16MHz
#define TIMER1_CONFIG_MODE         TIMER_MODE_MODE_Timer
#define TIMER1_CONFIG_BIT_WIDTH    TIMER_BITMODE_BITMODE_16Bit
#define TIMER1_CONFIG_IRQ_PRIORITY APP_IRQ_PRIORITY_LOW

#define TIMER1_INSTANCE_INDEX      (TIMER0_ENABLED)
#endif
 
#define TIMER2_ENABLED 0

#if (TIMER2_ENABLED == 1)
#define TIMER2_CONFIG_FREQUENCY    NRF_TIMER_FREQ_16MHz
#define TIMER2_CONFIG_MODE         TIMER_MODE_MODE_Timer
#define TIMER2_CONFIG_BIT_WIDTH    TIMER_BITMODE_BITMODE_16Bit
#define TIMER2_CONFIG_IRQ_PRIORITY APP_IRQ_PRIORITY_LOW

#define TIMER2_INSTANCE_INDEX      (TIMER1_ENABLED+TIMER0_ENABLED)
#endif

#define TIMER3_ENABLED 0

#if (TIMER3_ENABLED == 1)
#define TIMER3_CONFIG_FREQUENCY    NRF_TIMER_FREQ_16MHz
#define TIMER3_CONFIG_MODE         TIMER_MODE_MODE_Timer
#define TIMER3_CONFIG_BIT_WIDTH    TIMER_BITMODE_BITMODE_16Bit
#define TIMER3_CONFIG_IRQ_PRIORITY APP_IRQ_PRIORITY_LOW

#define TIMER3_INSTANCE_INDEX      (TIMER2_ENABLED+TIMER1_ENABLED+TIMER0_ENABLED)
#endif

#define TIMER4_ENABLED 0

#if (TIMER4_ENABLED == 1)
#define TIMER4_CONFIG_FREQUENCY    NRF_TIMER_FREQ_16MHz
#define TIMER4_CONFIG_MODE         TIMER_MODE_MODE_Timer
#define TIMER4_CONFIG_BIT_WIDTH    TIMER_BITMODE_BITMODE_16Bit
#define TIMER4_CONFIG_IRQ_PRIORITY APP_IRQ_PRIORITY_LOW

#define TIMER4_INSTANCE_INDEX      (TIMER3_ENABLED+TIMER2_ENABLED+TIMER1_ENABLED+TIMER0_ENABLED)
#endif


#define TIMER_COUNT (TIMER0_ENABLED + TIMER1_ENABLED + TIMER2_ENABLED + TIMER3_ENABLED + TIMER4_ENABLED)

/* RTC */
#define RTC0_ENABLED 0

#if (RTC0_ENABLED == 1)
#define RTC0_CONFIG_FREQUENCY    32678
#define RTC0_CONFIG_IRQ_PRIORITY APP_IRQ_PRIORITY_LOW
#define RTC0_CONFIG_RELIABLE     false

#define RTC0_INSTANCE_INDEX      0
#endif

#define RTC1_ENABLED 0

#if (RTC1_ENABLED == 1)
#define RTC1_CONFIG_FREQUENCY    32768
#define RTC1_CONFIG_IRQ_PRIORITY APP_IRQ_PRIORITY_LOW
#define RTC1_CONFIG_RELIABLE     false

#define RTC1_INSTANCE_INDEX      (RTC0_ENABLED)
#endif

#define RTC_COUNT                (RTC0_ENABLED+RTC1_ENABLED)

#define NRF_MAXIMUM_LATENCY_US 2000

/* RNG */
#define RNG_ENABLED 0

#if (RNG_ENABLED == 1)
#define RNG_CONFIG_ERROR_CORRECTION true
#define RNG_CONFIG_POOL_SIZE        8
#define RNG_CONFIG_IRQ_PRIORITY     APP_IRQ_PRIORITY_LOW
#endif

/* PWM */

#define PWM0_ENABLED 0

#if (PWM0_ENABLED == 1)
#define PWM0_CONFIG_OUT0_PIN        2
#define PWM0_CONFIG_OUT1_PIN        3
#define PWM0_CONFIG_OUT2_PIN        4
#define PWM0_CONFIG_OUT3_PIN        5
#define PWM0_CONFIG_IRQ_PRIORITY    APP_IRQ_PRIORITY_LOW
#define PWM0_CONFIG_BASE_CLOCK      NRF_PWM_CLK_1MHz
#define PWM0_CONFIG_COUNT_MODE      NRF_PWM_MODE_UP
#define PWM0_CONFIG_TOP_VALUE       1000
#define PWM0_CONFIG_LOAD_MODE       NRF_PWM_LOAD_COMMON
#define PWM0_CONFIG_STEP_MODE       NRF_PWM_STEP_AUTO

#define PWM0_INSTANCE_INDEX 0
#endif

#define PWM1_ENABLED 0
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

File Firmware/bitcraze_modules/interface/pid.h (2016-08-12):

/**
 *    ||          ____  _ __
 * +------+      / __ )(_) /_______________ _____  ___
 * | 0xBC |     / __  / / __/ ___/ ___/ __ `/_  / / _ \
 * +------+    / /_/ / / /_/ /__/ /  / /_/ / / /_/  __/
 *  ||  ||    /_____/_/\__/\___/_/   \__,_/ /___/\___/
 *
 * Crazyflie control firmware
 *
 * Copyright (C) 2011-2012 Bitcraze AB
 *
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
 *
 * pid.h - implementation of the PID regulator
 */
#ifndef PID_H_
#define PID_H_

#include <stdbool.h>
#include <stdint.h>
#include <string.h>

#include "nordic_common.h"

#define ANGLE_KP_COMMON 4 //def 3.5
#define RATE_KP_COMMON 70 // def 70

#define PITCH_ROLL_RATE_KP 70
#define PITCH_ROLL_RATE_KI 2
#define PITCH_ROLL_RATE_KD 10

#define PITCH_ROLL_KP 40
#define PITCH_ROLL_KI 0
#define PITCH_ROLL_KD 0

#define INTEGRAL_SCALER 500
#define DERIVATOR_SCALER 100

#define PID_ROLL_RATE_KP  PITCH_ROLL_RATE_KP
#define PID_ROLL_RATE_KI  PITCH_ROLL_RATE_KI
#define PID_ROLL_RATE_KD  PITCH_ROLL_RATE_KD
#define PID_ROLL_RATE_INTEGRATION_LIMIT    33.3

#define PID_PITCH_RATE_KP  PITCH_ROLL_RATE_KP
#define PID_PITCH_RATE_KI  PITCH_ROLL_RATE_KI
#define PID_PITCH_RATE_KD  PITCH_ROLL_RATE_KD
#define PID_PITCH_RATE_INTEGRATION_LIMIT   33.3

#define PID_YAW_RATE_KP  70
#define PID_YAW_RATE_KI  0 //16.7
#define PID_YAW_RATE_KD  0.0
#define PID_YAW_RATE_INTEGRATION_LIMIT     33.3

#define PID_ROLL_KP  PITCH_ROLL_KP
#define PID_ROLL_KI  PITCH_ROLL_KI
#define PID_ROLL_KD  PITCH_ROLL_KD
#define PID_ROLL_INTEGRATION_LIMIT    20.0

#define PID_PITCH_KP  PITCH_ROLL_KP
#define PID_PITCH_KI  PITCH_ROLL_KI
#define PID_PITCH_KD  PITCH_ROLL_KI
#define PID_PITCH_INTEGRATION_LIMIT   20.0

#define PID_YAW_KP  60
#define PID_YAW_KI 50 //1.0
#define PID_YAW_KD  90
#define PID_YAW_INTEGRATION_LIMIT     360.0

#define PID_ALT_KP	PID_YAW_KP
#define PID_ALT_KI	PID_YAW_KI
#define PID_ALT_KD	PID_YAW_KD
#define PID_ALT_INTEGRATION_LIMIT			33.3

#define DEFAULT_PID_INTEGRATION_LIMIT  5000.0

typedef struct
{
  float desired;      //< set point
  float error;        //< error
  float prevError;    //< previous error
  float integ;        //< integral
  float deriv;        //< derivative
  float kp;           //< proportional gain
  float ki;           //< integral gain
  float kd;           //< derivative gain
  float outP;         //< proportional output (debugging)
  float outI;         //< integral output (debugging)
  float outD;         //< derivative output (debugging)
  float iLimit;       //< integral limit
  float iLimitLow;    //< integral limit
  float dt;           //< delta-time dt
} PidObject;

/**
 * PID object initialization.
 *
 * @param[out] pid   A pointer to the pid object to initialize.
 * @param[in] desired  The initial set point.
 * @param[in] kp        The proportional gain
 * @param[in] ki        The integral gain
 * @param[in] kd        The derivative gain
 */
void pidInit(PidObject* pid, const float desired, const float kp,
             const float ki, const float kd, const float dt);

/**
 * Set the integral limit for this PID in deg.
 *
 * @param[in] pid   A pointer to the pid object.
 * @param[in] limit Pid integral swing limit.
 */
void pidSetIntegralLimit(PidObject* pid, const float limit);

/**
 * Reset the PID error values
 *
 * @param[in] pid   A pointer to the pid object.
 * @param[in] limit Pid integral swing limit.
 */
void pidReset(PidObject* pid);

/**
 * Update the PID parameters.
 *
 * @param[in] pid         A pointer to the pid object.
 * @param[in] measured    The measured value
 * @param[in] updateError Set to TRUE if error should be calculated.
 *                        Set to False if pidSetError() has been used.
 * @return PID algorithm output
 */
float pidUpdate(PidObject* pid, const float measured, const bool updateError);

/**
 * Set a new set point for the PID to track.
 *
 * @param[in] pid   A pointer to the pid object.
 * @param[in] angle The new set point
 */
void pidSetDesired(PidObject* pid, const float desired);

/**
 * Set a new set point for the PID to track.
 * @return The set point
 */
float pidGetDesired(PidObject* pid);

/**
 * Find out if PID is active
 * @return TRUE if active, FALSE otherwise
 */
bool pidIsActive(PidObject* pid);

/**
 * Set a new error. Use if a special error calculation is needed.
 *
 * @param[in] pid   A pointer to the pid object.
 * @param[in] error The new error
 */
void pidSetError(PidObject* pid, const float error);

/**
 * Set a new proportional gain for the PID.
 *
 * @param[in] pid   A pointer to the pid object.
 * @param[in] kp    The new proportional gain
 */
void pidSetKp(PidObject* pid, const float kp);

/**
 * Set a new integral gain for the PID.
 *
 * @param[in] pid   A pointer to the pid object.
 * @param[in] ki    The new integral gain
 */
void pidSetKi(PidObject* pid, const float ki);

/**
 * Set a new derivative gain for the PID.
 *
 * @param[in] pid   A pointer to the pid object.
 * @param[in] kd    The derivative gain
 */
void pidSetKd(PidObject* pid, const float kd);

/**
 * Set a new dt gain for the PID. Defaults to IMU_UPDATE_DT upon construction
 *
 * @param[in] pid   A pointer to the pid object.
 * @param[in] dt    Delta time
 */
void pidSetDt(PidObject* pid, const float dt);

uint8_t * get_default(void);

#endif /* PID_H_ */

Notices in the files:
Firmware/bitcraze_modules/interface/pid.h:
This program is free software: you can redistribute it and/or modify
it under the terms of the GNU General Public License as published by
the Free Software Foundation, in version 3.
